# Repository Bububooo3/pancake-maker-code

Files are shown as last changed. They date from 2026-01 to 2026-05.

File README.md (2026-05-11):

# AUTOMATIC PANCAKE MAKER

## JACKSON LOSSIUS, RICHARD SCOTT

---

final product

---

<details>
  <summary>See Video Demo</summary>
  
  https://github.com/user-attachments/assets/425521ff-0307-458f-a22e-615c610f6d97
  
  </details>

<br>

[See electrical diagram](https://github.com/Bububooo3/Automatic-Pancake-Maker/blob/main/Diagrams/Pancake%20Maker%20Wiring%20Diagram.pdf)

---

> [!NOTE]
> For this project, we designed and constructed a machine that takes in batter and produces pancakes. The machine dispenses batter onto a heated conveyor belt, which moves the batter towards the exit slot based on a timer. A heated top conveyor belt above the pancake works with the heated conveyor on the bottom to squeeze the pancake and dispense it through this slot. The machine is well-insulated, and Arduino-driven electrical work can be concentrated below or next to the product. A user-interface on the machine lets users know what is happening and what they need to do using an LED strip and a LCD display.

---

# PROJECT OVERVIEW

> [!IMPORTANT]
> We’re providing a solution for hungry, busy engineering students and teachers who lack time to make food. Students can come early, stay late, and stay on task without leaving the lab for food breaks. Being able to make pancakes efficiently with a machine will help the Engineering Lab and Robotics team raise money through sales.

## Design Goals

- 1 pancake every 60 seconds  
- 20 minutes continuous functionality minimum  
- Insulation  
- Electronics must be sealed  
- Consistent size  
- Effective user interface  
- Fully cooked  
- Minimize burnt pancakes and debris  

## Constraints

- Time: must be completed by April 26th  
- Budget: must be inside a $800.00 budget  
- Space: must fit in the lab  
- Safety: must be properly contained, so it will not be a fire or electrical hazard  
- Must weigh less than 25 kg  

---

# RESOURCES

## POPCAKE

> We referenced the site and manual for the Popcake machine, which is a commercial pancake-maker sold mainly to hotels for $3000/unit.

## YOUTUBE

> We referenced YouTube videos to learn about electrical components, mechanical concepts, and using Arduino boards.

## AI

> We referenced AI (Anthropic’s Claude and Microsoft’s Copilot) to locate logic errors during the tedious and vital debugging process. While planning wiring, we used AI to help ensure safe design and make up for unfamiliarity with electrical engineering.

## ARTICLES & FORUMS

> We referenced online articles and forums regularly to sort out wiring issues, learn overall best practices, and develop design concepts.

## PROFESSIONALS

> We consulted our teacher, Mr. Fennesy, for guidance in all stages of the production process: researching, designing, building, and testing/iterating. Meeting with an engineer from Popcake helped us understand their machine and design an effective one ourselves. Our project mentor Mr. Wingfield helped us ensure our electrical work is safe and functional.

---

# LEARNED SKILLS

## JACKSON

- Researching and designing products  
- Technical drawings  
- Iterative design  
- Mechanical assembly  
- Operating belt sander, drill press, band saw, and other tools  

## RICHARD

- Embedded systems programming  
- Planning and constructing circuits  
- Identifying electrical components  
- Researching and designing products  
- Electrical safety procedures  

---

# CHALLENGES

- After choosing the project, conducting research was challenging, because there were not many existing automatic pancake makers to reference, and Popcake is very protective of product information.  
- Planning wiring and realizing that plan were both long and challenging iteration processes.  
- Designing the product was a challenging process. To avoid having to spend a large amount of time mastering CAD software, Jackson took advantage of his artistic skills to create technical drawings.  
- Ensuring user safety and maximizing cost efficiency were both challenging goals to achieve.  

---

# EVALUATION & ANALYSIS

## REFLECTION

> Like many of the projects, this automatic pancake-maker was a struggle to make from start to finish. Neither of us could’ve done it alone. Because of this struggle, every accomplished task felt like it was worth celebrating, and enduring and adapting to the process head-on meant getting to learn everything the project required of us by ourselves. Above all, it was an amazing learning experience and successful collaboration.

## MISTAKES

- Taking our time at the start  
- Going long periods doing respective tasks without communicating progress to each other  
- Waiting until the last week to build and test the final product  
- Procrastinating on tasks that seemed too difficult to accomplish  
- Forgetting to set the potentiometer on electrical components, resulting in smoke, melting, and explosions on multiple occasions.  
- Underestimating the project’s difficulty  
- Avoiding using AI to debug until there was little time left to code.  

---

# MECHANICAL BILL OF MATERIALS

- MyLifeUNIT Pancake Batter Dispenser, 40oz  
- Presto 07071 15-inch Electric Tilt-n-fold Griddle, Black  
- Amazon Grocery, Original Pancake and Waffle Mix, 32 oz  
- Betty Crocker Bisquick Shake 'n Pour, Buttermilk Pancake Mix, 5.1 oz  
- Krusteaz Light and Fluffy Buttermilk Complete Pancake Mix, Waffle and Pancake Mix, Just Add Water, 32 oz Box  
- Hungry Jack Complete Extra Light and Fluffy Pancake Mix and Waffle Mix, 32 oz Box  
- Great Value Complete Pancake & Waffle Mix, Extra Fluffy, Original, 32 oz  
- 24t x 15mm Wide Aluminum Pulley (HTD 5mm, 8mm1/2" hex Bore) (WCP-1803)  
- belts  
- bearings  
- Bearing plates  
- ceramic fireproof insulation  
- (Economy Geared Stepper Motor) Alloy Steel Mounting Bracket ST-M1  
- Mrs. Butterworth's Complete Buttermilk Pancake Mix, 32 oz  
- 3 Pack PTFE Teflon Sheet 16"x20"  
- Mrs. Butterworth's Complete Buttermilk Pancake Mix, 32 oz  
- Betty Crocker bisquick pancake mix  
- Mainstays 4 Cup PP Plastic Measuring Cup, 32 oz, Clear  
- Great Value Complete Pancake & Waffle Mix, Buttermilk, 32 oz  
- Mainstays Solid Kitchen Turner, Nylon, Black, Diamond Pattern Handle  
- GoodCook 4 Quart Stainless Steel Mixing Bowl  
- GoodCook Pro Measuring Cups And Spoons, Set Of 8 Nesting With Storage Ring  
- motor shaft adaptor to hex (shaft coupler)  
- 0.5 in. 7075 Aluminum Hex Shaft Stock. 3' x2  
- compliance wheels for conveyor belt  
- Steel supports  
- food grade high temp silicone  
- 10 pack ptfe sheets 12"x16"  
- high temp epoxy  
- Bonded #92 TeflonThread - UV Resistant and Heavy Duty Heat-Low Temperature Resistant Thread Sewing - Extra Strong Outdoor Thread - Can Be Used On Home Sewing Machine 600yds (White)

---

# ELECTRICAL BILL OF MATERIALS

- Heat Paste  
- Extension Cord  
- 220 Ω Resistor (In kit)  
- 470 Ω Resistor (In kit)  
- 1000 μF Capacitors (Capacitor Kit)  
- 100 μF Capacitors (In kit)  
- 12V DC Power Supply  
- Buck Converter (LM2596)  
- Solid State Relay  
- Dial Potentiometer Kit  
- Wago Connector Kit  
- Barrel Screw Adapter  
- In-line Fuse Holder  
- Nuts  
- Jumper Wires  
- Diodes  
- LCD 1602 (Standard Config)  
- MyLifeUNIT Pancake Batter Dispenser, 40oz  
- STEPPERONLINE NEMA 17 Stepper Motor (Economy Geared Stepper Motor) Alloy Steel Mounting Bracket ST-M1  
- Arduino Microcontroller  
- STEPPERONLINE NEMA 17 Stepper Motor (Economy Geared Stepper Motor) Alloy Steel Mounting Bracket ST-M1  
- 1 kΩ Resistor (Resistor Kit)  
- NeoPixel 8 LED Strip (WS2812B)  
- Arduino Mega 2560 (x2)  
- A4988 Stepper Motor Driver (w/ Heat Sinks)  
- Push Button Kit  
- LCD 1602 (Standard Config)  
- Star Washers  
- Ring Terminals  
- Flat Washers  
- Breadboards  

---

# MATH & PHYSICS INVOLVED

- Rotational Kinematics  
- Geometry  
- Arithmetic

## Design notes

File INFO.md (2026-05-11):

<h2>Automatic Pancake Maker</h2>

My first Arduino/electrical project! 

> Simulator diagrams don't match real thing, bc sims don't have necessary components or capabilities

View up-to-date hand-drawn diagram [here](https://github.com/Bububooo3/Automatic-Pancake-Maker/blob/main/Diagrams/Pancake%20Maker%20Wiring%20Diagram.pdf)

<hr>
  I did mostly electrical and software stuff and my partner Jackson does mostly mechanical and product design stuff. We worked together on a lot of stuff, too.
<hr>
<h3>Power Diagram</h3>

https://github.com/Bububooo3/pancake-maker-code/blob/main/Pancake%20Maker%20Electronic%20Diagram.pdf

<hr>
<h3>Wokwi ("Current" system)</h3>

https://wokwi.com/projects/449513725919513601

> Prototype: https://wokwi.com/projects/454495520037891073
>
> TinkerCAD: [(Outdated)](https://www.tinkercad.com/things/4bpHhnqHLCV-subsystem-wiring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)

<hr>

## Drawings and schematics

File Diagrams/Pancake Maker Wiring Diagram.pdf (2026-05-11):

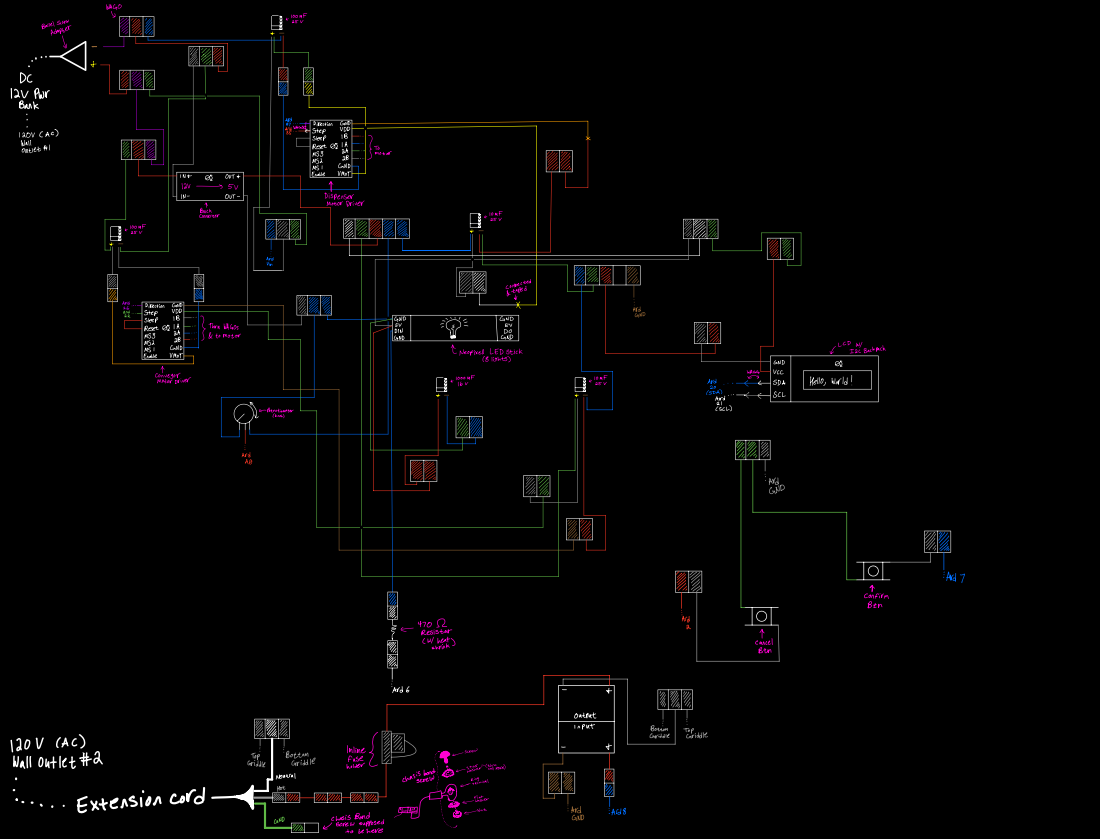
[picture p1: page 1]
Adapter; cPwr; askand; ND viaIB1Aat; unotDirection; step sleep reset mss mss enane us; I orIac; HetI; motor to; connerDriverBuck; one; suroom; Ara andand ND viaIB1Aat; GND; step sleep reset mss mss; enanex; and; inandANDso GND.turn; Do WAGos; Law LEDstick; Barrackneopixes; Iac islists andwaao.weconveyor notondriverroom; one suand; mar 2 And ascusHello a; world SDAcc; I sa potentiometer; can; Arato; Ard GND; Ard; confirm Ben; right left 1; vdots; nor; Adr; resistor; cutneat; shrinkcancel; Btn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

wagoroom suBarrel screw

inr V21in.outsoout.Dispenser motor
atomotor

vi.connected taped

output
Bottom Griddleinput Gridaetop

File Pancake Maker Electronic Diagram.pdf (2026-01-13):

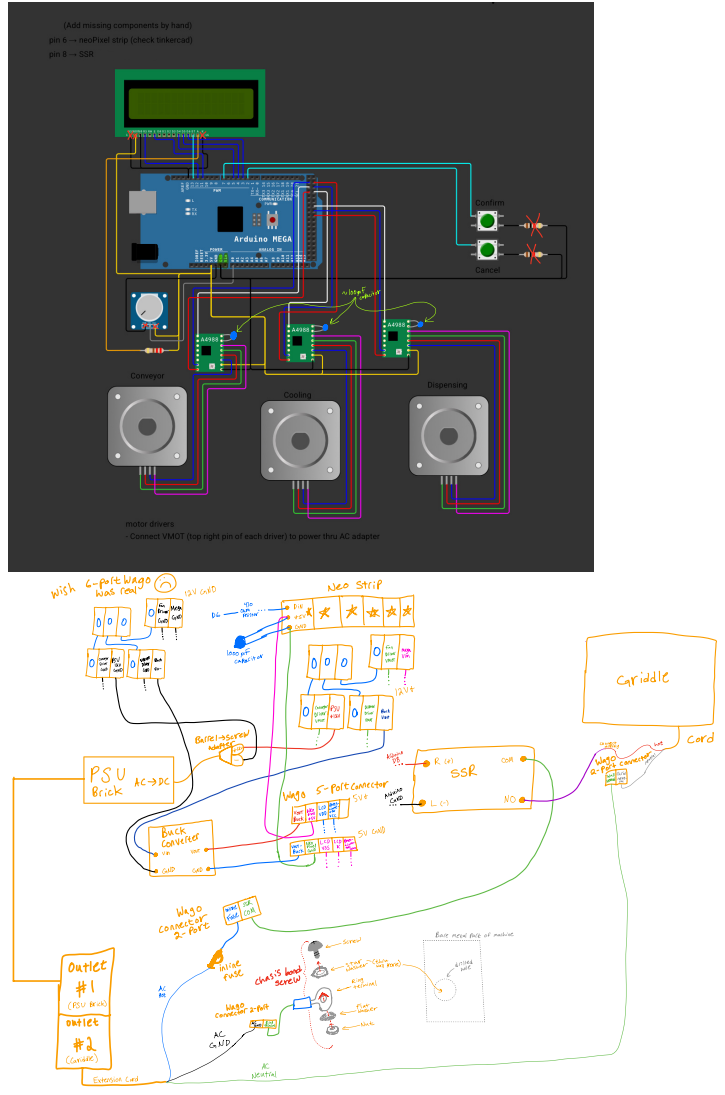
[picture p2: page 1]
lowdose; Paridae; III; neutral

wish68 ¹⁹,90
IBi.li iiIo.F iiiIii
Iii tiIiii
iiiiiiiii'itife.ae
isiii iiii
iIii
IEi

IiiiiiIiiii ii.it
iiiiiii ii

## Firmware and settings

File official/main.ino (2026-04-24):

#include <Adafruit_NeoPixel.h>
#include <LiquidCrystal_I2C.h>
#include <AccelStepper.h>
#include <Wire.h>

#include "Animations.h"
#include "Pins.h"
#include "Motors.h"
#include "Times.h"
#include "States.h"



/////////////////
/// VARIABLES ///
/////////////////
///////////////////////////////////////////////////////////////////////////////////////////
// Booleans //
bool confirmPressedPrev = LOW, cancelPressedPrev = LOW;  // Init button states
bool dispensingActive = false;                           // Init dispenser states
bool serviceMsg = false;                                 // Init service message state
bool griddleEnabled = false;                             // Init griddle state
bool griddleReady = true;                                // Init griddle state
bool griddleReadyPrev = true;                            // exactly what it sounds like
bool confirmStable = LOW;                                // more reliable input
bool cancelStable = LOW;                                 // more reliable input
bool tkA = false;                                        // is kill mode active
bool dispenserHoming = false;                            // is dispenser homing
bool heatOnBoot = true;                                  // Config
bool firstCake = false;
bool lastCake = false;

// Strings //
String lastPrintLCD1 = "";
String lastPrintLCD2 = "";
String placeholder = "                ";

// State Machine //
Status status = STATUS_REQUEST;

// Numbers //
int mlevel = 8;     // Maximum # pancakes we're able to make
int level = 1;      // Init # pancakes to make
int plevel = 0;     // Init previous # pancakes to make
int dispensed = 0;  // Init # pancakes dispensed

unsigned long t_bake, t_kill, t_griddle, t_dispense, t_confirmDebounce, t_cancelDebounce, t_lastCake;  // Init timers


//////////////////
/// COMPONENTS ///
//////////////////
///////////////////////////////////////////////////////////////////////////////////////////
// Initialize LCD: (Address, Column, Rows)
LiquidCrystal_I2C lcd(0x27, 16, 2);

// Initialize LED Strip: (#LEDs, Pin, Color Mode + Signal)
Adafruit_NeoPixel led(8, LEDPIN, NEO_GRB + NEO_KHZ800);

// Initialize stepper motors: (driver, STEP, DIR)
AccelStepper conveyor(AccelStepper::DRIVER, CONVEYORPIN_STEP, CONVEYORPIN_DIR);
AccelStepper dispenser(AccelStepper::DRIVER, DISPENSERPIN_STEP, DISPENSERPIN_DIR);
/* AccelStepper fan(AccelStepper::DRIVER, 25, 23); */

///////////////////////////////////////////////////////////////////////////////////////////



////////////////////////////////////
/// LIBRARY-DEPENDENT CONSTANTS ////
////////////////////////////////////
///////////////////////////////////////////////////////////////////////////////////////////
// Colors
#define WHITE led.Color(255, 255, 255)
#define RED led.Color(255, 0, 0)
#define GREEN led.Color(0, 255, 0)
#define BLUE led.Color(0, 0, 255)
#define YELLOW led.Color(255, 255, 0)
#define CYAN led.Color(0, 255, 255)
#define MAGENTA led.Color(255, 0, 255)
#define ORANGE led.Color(255, 165, 0)
#define PURPLE led.Color(128, 0, 128)
#define OFF 0

// Presets
const uint32_t warning[8] = { YELLOW, ORANGE, YELLOW, ORANGE, YELLOW, ORANGE, YELLOW, ORANGE };
const uint32_t danger[8] = { RED, RED, RED, RED, RED, RED, RED, RED };
const uint32_t rqst[8] = { PURPLE, MAGENTA, PURPLE, MAGENTA, PURPLE, MAGENTA, PURPLE, MAGENTA };
const uint32_t dormant[8] = { BLUE, WHITE, BLUE, WHITE, BLUE, WHITE, BLUE, WHITE };
const uint32_t off[8] = { OFF, OFF, OFF, OFF, OFF, OFF, OFF, OFF };
const uint32_t valid[8] = { GREEN, GREEN, GREEN, GREEN, GREEN, GREEN, GREEN, GREEN };
uint32_t prevLED[8] = { OFF, OFF, OFF, OFF, OFF, OFF, OFF, OFF };

////////////////////////////////////////////////////////////////////////////////////////



/////////////////
/// FUNCTIONS ///
/////////////////
////////////////////////////////////////////////////////////////////////////////////////////
// Macros
#define getArraySize(a) (sizeof(a) / sizeof((a)[0]))

// Center/truncate string (16 characters)
String center(String msg) {
  return (msg.length() <= 16) ? placeholder.substring(0, (16 - msg.length()) / 2) + msg : msg.substring(0, 16);
}


// Display string on LCD
bool printMessage(String msg, int line = 0) {
  if (line) {
    if (lastPrintLCD2 == msg) {
      return false;
    }
  } else {
    if (lastPrintLCD1 == msg) {
      return false;
    }
  }

  line = constrain(line, 0, 1);
  lcd.setCursor(0, line);
  lcd.print(placeholder);
  lcd.setCursor(0, line);
  lcd.print(msg);

  if (line) {
    lastPrintLCD2 = msg;
  } else {
    lastPrintLCD1 = msg;
  }

  return true;
}


// Clear LCD line or entire screen if no params
bool clearLine(int lvl = -1) {
  if (lvl < 0) {
    lcd.clear();
    lastPrintLCD1 = "";
    lastPrintLCD2 = "";
    return true;
  }

  lvl = constrain(lvl, 0, 1);
  printMessage(placeholder, lvl);
  return true;
}


// Return whether the previous LED is the same as the current one
bool getLEDUnchanged(const uint32_t a[]) {
  return (
    prevLED[0] == a[0] && prevLED[1] == a[1] && prevLED[2] == a[2] && prevLED[3] == a[3] && prevLED[4] == a[4] && prevLED[5] == a[5] && prevLED[6] == a[6] && prevLED[7] == a[7]);
}

void setLEDChanged(const uint32_t a[]) {
  prevLED[0] = a[0];
  prevLED[1] = a[1];
  prevLED[2] = a[2];
  prevLED[3] = a[3];
  prevLED[4] = a[4];
  prevLED[5] = a[5];
  prevLED[6] = a[6];
  prevLED[7] = a[7];
}


// Set LED strip colors manually
bool setColors(int a = OFF, int b = OFF, int c = OFF, int d = OFF, int e = OFF, int f = OFF, int g = OFF, int h = OFF) {
  led.setPixelColor(0, a);
  led.setPixelColor(1, b);
  led.setPixelColor(2, c);
  led.setPixelColor(3, d);
  led.setPixelColor(4, e);
  led.setPixelColor(5, f);
  led.setPixelColor(6, g);
  led.setPixelColor(7, h);

  uint32_t temp[8] = { a, b, c, d, e, f, g, h };
  setLEDChanged(temp);

  led.show();
  return true;
}


// Set LED strip colors using a preset
bool floodColors(const uint32_t z[8]) {
  setColors(z[0], z[1], z[2], z[3], z[4], z[5], z[6], z[7]);
  return true;
}


// Disable LED strip lights efficiently
bool disableLED() {
  led.setPixelColor(0, OFF);
  led.setPixelColor(1, OFF);
  led.setPixelColor(2, OFF);
  led.setPixelColor(3, OFF);
  led.setPixelColor(4, OFF);
  led.setPixelColor(5, OFF);
  led.setPixelColor(6, OFF);
  led.setPixelColor(7, OFF);
  led.show();
  return true;
}


// Set fan motor pulse rate
void setFanPower(float i) {
  // <disabled> fan.setSpeed(MAXSTEP * constrain(i, 0, 1));
}


// Get the net difference between these two times in milliseconds
unsigned long difftime(unsigned long t1, unsigned long t2) {
  return (t2 >= t1) ? (t2 - t1) : (0xFFFFFFFFUL - t1 + t2 + 1);  // ~49-day lifetime of accuracy
}

////////////////////////////////////////////////////////////////////////////////////////



/////////////////
// ABSTRACTION //
/////////////////
////////////////////////////////////////////////////////////////////////////////////////////
// EXTRA INTERFACE CONSTANTS (for optimization, convenience & such)
const String spsMsg = "Pancakes";  // Word to show for >1 pancakes
const String amt = "Auto-Mode";    // Word to show for auto mode

const String bMsg = center("Baking");

const String eMsg1 = center("Action");      // Cancel display line 1
const String eMsg2 = center("Terminated");  // Cancel display line 2

const String rMsg1 = center("Pancakes");
const String rMsg2 = center("Ready");

void bakeComplete();  // Just in case

// QoL method
bool isActive(Status check) {
  return (status == check);
}

void setActive(Status check) {
  status = check;
}

// Display a message on LCD asking for # pancakes (and set requesting to true simultaneously)
void requestNumPancakes() {
  setActive(STATUS_REQUEST);
  printMessage(center("Bake how many?"));
  clearLine(1);
}


// Set whether the griddle should be heating up or cooling down or neither
void setGriddleEnabled(bool enabled) {
  if (griddleEnabled == enabled) {
    return;
  }

  digitalWrite(GRIDPIN, enabled);
  griddleEnabled = enabled;
  griddleReady = false;
  t_griddle = millis();
}


// Update griddle per heartbeat w/o yielding program
// Returns true if griddle is fully cooled or heated
bool updateGriddle() {
  unsigned long elapsed = difftime(t_griddle, millis());
  bool canWriteLCD = !isActive(STATUS_READY) && !isActive(STATUS_CANCEL);

  if (griddleEnabled) {
    if (canWriteLCD) {
      int frame = static_cast<int>(elapsed / ANIMINC) % getArraySize(heatingAnim);
      printMessage(center(heatingAnim[frame]), 1);
    }
    if (!griddleReady && elapsed >= HEATUP) {
      griddleReady = true;
      if (isActive(STATUS_BAKE)) t_dispense = millis();
      return true;
    }
  } else {
    if (canWriteLCD) {
      int frame = static_cast<int>(elapsed / ANIMINC) % getArraySize(coolingAnim);
      printMessage(center(coolingAnim[frame]), 1);
    }
    if (!griddleReady && elapsed >= COOLDOWN) {
      griddleReady = true;
      return true;
    }
  }
  return false;
}

// The entire warm-up process for the machine w/ animations
void introductionProtocol() {
  for (int i = 0; (i < getArraySize(intro)); i++) {
    printMessage(center(intro[i]));
    delay(ANIMINC);
  }

  printMessage(center("By Jesuit HS"), 1);
  delay(MSGWAIT);
  clearLine();

  setFanPower(1.0f);

  if (heatOnBoot) {
    setGriddleEnabled(true);
  }

  printMessage(center("[Complete]"), 1);
  delay(MSGWAIT);
  clearLine();
}


// For handling during cancel state or errors
void homeDispenser() {
  dispensingActive = false;
  dispenserHoming = true;
  dispenser.moveTo(DISPENSERCLOSE);
}

// Dispense pancakes fxn
bool dispense() {
  if (dispenserHoming) {
    if (dispenser.distanceToGo() == 0 && dispenser.currentPosition() == DISPENSERCLOSE) {
      dispenserHoming = false;
    }
    return false;
  }

  if (!dispensingActive) return false;

  if (dispensed >= level) return false;

  if (dispenser.distanceToGo() == 0) {
    if (dispenser.currentPosition() == DISPENSEROPEN) {
      dispenser.moveTo(DISPENSERCLOSE);
    } else if (dispenser.currentPosition() == DISPENSERCLOSE) {
      dispensingActive = false;
      dispenser.setCurrentPosition(dispenser.currentPosition());
      return true;
    }
  }
  return false;
}


// Handle the confirm/cancel button logic
void handleButtons() {
  bool rawConfirm = (digitalRead(CONFIRMPIN) == LOW);
  bool rawCancel = (digitalRead(CANCELPIN) == LOW);

  unsigned long now = millis();

  // CONFIRM DEBOUNCE
  if (rawConfirm != confirmStable) {
    if (now - t_confirmDebounce >= DEBOUNCE) {
      confirmStable = rawConfirm;
      t_confirmDebounce = now;  // Reset only after committing
    }
  }

  // CANCEL DEBOUNCE
  if (rawCancel != cancelStable) {
    if (now - t_cancelDebounce >= DEBOUNCE) {
      cancelStable = rawCancel;
      t_cancelDebounce = now;  // Reset only after committing
    }
  }

  bool confirmPressed = confirmStable;
  bool cancelPressed = cancelStable;

  // Confirm button pressed
  if (!confirmPressedPrev && confirmPressed) {
    switch (status) {
      case STATUS_CANCEL:
        setActive(STATUS_REQUEST);
        t_kill = 0;
        tkA = false;
        lastCake = false;
        clearLine();
        printMessage(center("[please wait]"));
        plevel = -1;
        break;

      case STATUS_REQUEST:
        level = map(analogRead(A0), 0, 1023, 1, mlevel);
        if (!heatOnBoot) setGriddleEnabled(true);

        t_bake = now;
        t_dispense = now;
        griddleReadyPrev = false;
        dispensingActive = false;
        dispenserHoming = false;
        lastCake = false;
        dispensed = 0;

        clearLine();
        firstCake = true;
        setActive(STATUS_BAKE);
        break;

      case STATUS_READY:
        setActive(STATUS_REQUEST);
        break;
    }
  }

  // Cancel button pressed
  if (cancelPressed && !cancelPressedPrev) {
    setActive(STATUS_CANCEL);

    if (!heatOnBoot) {
      setGriddleEnabled(false);
    }

    homeDispenser();
    clearLine();
    t_kill = millis();
    tkA = true;
    lastCake = false;
    t_confirmDebounce = millis();
  }

  // Baking System
  conveyor.setSpeed(isActive(STATUS_BAKE) ? CONVEYORSTEP : 0);
  // <disabled> fan.setSpeed(isActive(STATUS_BAKE) ? MAXSTEP : 0);

  // Store state
  confirmPressedPrev = confirmPressed;
  cancelPressedPrev = cancelPressed;
}


void updateMotors() {
  conveyor.runSpeed();
  bool cycleComplete = dispense();
  dispenser.run();

  if (!griddleReady) {
    updateGriddle();
    griddleReadyPrev = false;
  } else {
    griddleReadyPrev = true;
  }

  serviceMsg = !griddleReady;

  if (!isActive(STATUS_BAKE)) return;

  if (cycleComplete) {
    dispensed++;
    t_dispense = millis();

    if (level < mlevel && dispensed >= level) {
      lastCake = true;
      t_lastCake = millis();
      return;
    }
  }

  if (lastCake && difftime(t_lastCake, millis()) >= COOKTIME) {
    lastCake = false;
    bakeComplete();
    return;
  }

  if (level == mlevel && difftime(t_bake, millis()) >= AUTOTIMEOUT) bakeComplete();
}

// Update per heartbeat fxn
void heartbeat() {
  t_bake = isActive(STATUS_BAKE) ? t_bake : 0UL;
  t_dispense = isActive(STATUS_BAKE) ? t_dispense : 0UL;
  t_kill = (isActive(STATUS_CANCEL) && tkA) ? t_kill : 0UL;

  handleButtons();
  updateMotors();
}


// The screen for asking for pancakes
void requestScreen() {
  // Map 0-1023 :: 1–mlevel
  level = map(analogRead(A0), 0, 1023, 1, mlevel);

  printMessage(center("Bake how many?"));

  // Choose # Pancakes Screen
  if ((abs(level - plevel) >= 1) && isActive(STATUS_REQUEST)) {
    if (level < mlevel) {
      printMessage(center(String(level * 2) + " " + spsMsg), 1);
    } else {
      printMessage(center(amt), 1);
    }

    plevel = level;
  }
}


// Runs when baking is finished
void bakeComplete() {
  setActive(STATUS_READY);
  if (!heatOnBoot) {
    setGriddleEnabled(false);
  }
}

// Display while baking
void bakeScreen() {
  if (!griddleReadyPrev) {
    printMessage(center("Heating..."));
    return;
  }

  printMessage(bMsg);
  printMessage((level < mlevel) ? center(String(level * 2) + " " + spsMsg) : center(amt), 1);

  if (!lastCake && ((firstCake) || (!dispensingActive && !dispenserHoming && (difftime(t_dispense, millis()) >= COOKTIME)))) {
    firstCake = false;
    dispensingActive = true;
    dispenser.moveTo(DISPENSEROPEN);
  }
}

// Display for when the pancakes are ready
void readyScreen() {
  printMessage(rMsg1);
  printMessage(rMsg2, 1);
}

////////////////////////////////////////////////////////////////////////////////////////



/////////////
// RUNTIME //
/////////////
////////////////////////////////////////////////////////////////////////////////////////
// Run once on boot
void setup() {
  // Pin Initialization
  pinMode(CONFIRMPIN, INPUT_PULLUP);
  pinMode(CANCELPIN, INPUT_PULLUP);
  pinMode(LEDPIN, OUTPUT);
  pinMode(GRIDPIN, OUTPUT);

  // LCD
  lcd.init();
  lcd.backlight();

  // LED
  led.begin();
  led.show();
  introductionProtocol();

  // Serial.begin(9600);

  // Stepper Motors
  conveyor.setMaxSpeed(CONVEYORSTEP);
  conveyor.setAcceleration(400);
  digitalWrite(CONVEYORPIN_DIR, ((CONVEYOR_INVERT) ? HIGH : LOW));
  digitalWrite(DISPENSERPIN_DIR, ((DISPENSER_INVERT) ? HIGH : LOW));
  // <disabled> fan.setMaxSpeed(MAXSTEP);
  dispenser.setMaxSpeed(DISPENSERSPEED);
  dispenser.setAcceleration(DISPENSERACCEL);

  dispenserHoming = true;
  dispenser.setCurrentPosition(dispenser.currentPosition());
  // while (dispenser.distanceToGo() != 0) dispenser.run();
  dispenserHoming = false;

  // Initialize griddle bc of heatOnBoot
  griddleReadyPrev = griddleReady;
}


// Run repeatedly
void loop() {
  heartbeat();

  // Light handling
  switch (status) {
    case STATUS_READY:
      // if (getLEDUnchanged(valid)) break;
      floodColors(valid);
      break;

    case STATUS_REQUEST:
      // if (getLEDUnchanged(rqst)) break;
      floodColors(rqst);
      break;

    case STATUS_BAKE:
      // if (getLEDUnchanged(warning)) break;
      floodColors(warning);
      break;

    case STATUS_CANCEL:
      // if (getLEDUnchanged(danger)) break;
      floodColors(danger);
      break;

    case STATUS_EMPTY:
      // if (getLEDUnchanged(dormant)) break;
      floodColors(dormant);
      break;
  }

  // Main logic handling
  if (serviceMsg && !isActive(STATUS_CANCEL) && !isActive(STATUS_BAKE) && !isActive(STATUS_READY)) return;

  switch (status) {
    case STATUS_CANCEL:
      printMessage(eMsg1);
      printMessage(eMsg2, 1);

      if (tkA && difftime(t_kill, millis()) >= KILLTIMEOUT) {
        tkA = false;
        clearLine();
        requestNumPancakes();
      }
      break;

    case STATUS_REQUEST:
      requestScreen();
      break;

    case STATUS_BAKE:
      bakeScreen();
      break;

    case STATUS_READY:
      readyScreen();
      break;

    case STATUS_EMPTY:
      requestNumPancakes();
      break;

    default:
      setActive(STATUS_EMPTY);
      break;
  }
}

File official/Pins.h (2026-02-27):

#ifndef PINS_H
#define PINS_H

// Button pins
const int CONFIRMPIN = 7;  // Confirm
const int CANCELPIN = 2;   // Cancel


// Appliance pins
const int LEDPIN = 6;   // For the NeoPixel strip
const int GRIDPIN = 8;  // For the SSR controlling the griddle


// Conveyor pins
const int CONVEYORPIN_STEP = 22;  // Step
const int CONVEYORPIN_DIR = 26;   // Direction


// Dispenser pins
const int DISPENSERPIN_STEP = 35;  // Step
const int DISPENSERPIN_DIR = 37;   // Direction

#endif

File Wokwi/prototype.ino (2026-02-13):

#include <Adafruit_NeoPixel.h>
#include <LiquidCrystal_I2C.h>
#include <AccelStepper.h>
#include <Wire.h>

/*
  PINS

  LCD w/ I2C Backpack:
	VCC 	→ 	5V
  GND 	→ 	GND
  SDA 	→ 	20
  SCL 	→ 	21


  Knob Potentiometer:
	GND		→		GND
	SIG		→		A0
	VCC		→		5V


  Conveyor Driver <Conveyor Stepper Motor Pin>:
	EN		→		24
	STEP	→		22
	DIR		→		26

	GND.2	→		GND

	2B		→		<B->
	2A		→		<A->
	1A		→		<A+>
	1B		→		<B+>

	VDD		→		5V
	GND.1	→		GND]


  Confirm Push Button:
	1:1 L	→		7
	1:2 R	→		GND


  Cancel Push Button:
	1:1 L	→		2
	1:2 R	→		GND
*/

/*
 	  ////////////////////////////////
	 // CONCERNING HEATING ELEMENT //
	////////////////////////////////
  ///////////////////////////////////////////////////////////////////////////////////////////
  > TinkerCAD sim doesn't support AC in the way needed for the griddle
  > For the real product, replace MOSFET w/ a solid-state relay (SSR)
  > The DC power supply represents the AC mains
  > Use SSR rated >=15A @ 120V AC
  > Ask mentor/electrician if unsure

  /////////////////////////////////////////////////////
  Reference Link
  > https://shorturl.fm/pwcKO

  /////////////////////////////////////////////////////
  Step-by-step Replacement Process:
  12V DC Power Suppy || 120V AC Outlet
  MOSFET			   ||  Solid-state relay
  - Cut only hot wire of extension cord
  - On the SSR, connect one end to COM & other to NO
  - Griddle turns on when relay is on & off when relay is off
  - DO NOT CUT NEUTRAL WIRE
  - We can control T using PID , maybe if we have time
  	^ (Not a necessity)
    ^ (Using rate of change, current T, target T, & time passed)

  /////////////////////////////////////////////////////
  Griddle Details (1200 Watt)
  > 2 prongs/wires (non-grounded)
  - Narrow blade: Hot(live) --> often black
  - Wide blade: Neutral --> often white
  > Hot wire carries 120V AC
  - Use an extension cord. Don't cut griddle cord directly.
  - Cut cord jacket carefully & strip hot wire after cutting it.

*/



/////////////
// GLOBALS //
/////////////
///////////////////////////////////////////////////////////////////////////////////////////
// bool baking = false, requesting = false, cancelMode = false, ready = false;
bool confirmPressedPrev = LOW, cancelPressedPrev = LOW;
bool griddleEnabled = false, griddleReady = true, heatOnBoot = false, serviceMsg = false;
String lastPrintLCD1 = "";
String lastPrintLCD2 = "";
String placeholder = "                ";
int level = 1;
int plevel = 0;
int dispensed = 0;
unsigned long t_bake, t_kill, t_griddle, t_dispense;

///////////////////////////////////////////////////////////////////////////////////////////


///////////////
// CONSTANTS //
///////////////
///////////////////////////////////////////////////////////////////////////////////////////
// Counts
// #define LEDCOUNT 8

// Time Lengths (milliseconds)
#define HEATUP 2e3
#define COOLDOWN 2e3
#define KILLTIMEOUT 60e3
#define MSGWAIT 1.5e3
#define ANIMINC 0.25e3
#define COOKTIME 10e3

// Step pulse rate (steps/second)
#define MAXSTEP 800.0
#define CONVEYORSTEP 800.0
// #define DISPENSERSPEED 800.0
// #define DISPENSERACCEL 400.0

// Step positions (Usually 1.8°/step, 200 steps/revolution)	← <Research more based on specific motor>
#define DISPENSEROPEN 0
#define DISPENSERCLOSE 0

// Dispenser states
#define OPENING true
#define CLOSING false

// Buttons
#define CONFIRMPIN 7
#define CANCELPIN 2

// Appliances
// #define LEDPIN 6
// #define GRIDPIN 8
#define CONVEYORPIN_EN 24
// #define COOLINGPIN_EN 27
// #define DISPENSERPIN_EN 33


// State Machine
enum Status {
  STATUS_EMPTY,
  STATUS_REQUEST,
  STATUS_BAKE,
  STATUS_CANCEL,
  STATUS_READY
};

Status status = STATUS_EMPTY;

// Fixed-Size Arrays
const char intro[][16] = {
  "pancake maker",
  "pAncake maker",
  "paNcake maker",
  "panCake maker",
  "pancAke maker",
  "pancaKe maker",
  "pancakE maker",
  "pancake Maker",
  "pancake mAker",
  "pancake maKer",
  "pancake makEr",
  "pancake makeR",
  " ",
};

const char heatingAnim[][16] = {
  "heating",
  "heating.",
  "heating..",
  "heating...",
  "heating",
};

const char coolingAnim[][16] = {
  "cooling",
  "cooling.",
  "cooling..",
  "cooling...",
  "cooling",
};
///////////////////////////////////////////////////////////////////////////////////////////




///////////////////////////
// INITIALIZE COMPONENTS //
///////////////////////////
///////////////////////////////////////////////////////////////////////////////////////////
// Initialize LCD: (RS, E, D4, D5, D6, D7)
// Initialize LED Strip: (#LEDs, Pin, Color Mode + Signal)
// Initialize stepper motors: (driver, STEP, DIR)

LiquidCrystal_I2C lcd(0x27, 16, 2);
// Adafruit_NeoPixel led(LEDCOUNT, LEDPIN, NEO_GRB + NEO_KHZ800);
AccelStepper conveyor(AccelStepper::DRIVER, 22, 26);
// <disabled> AccelStepper fan(AccelStepper::DRIVER, 25, 23);
// AccelStepper dispenser(AccelStepper::DRIVER, 35, 37);

///////////////////////////////////////////////////////////////////////////////////////////



////////////////////////////////
// LIBRARY-SPECIFIC CONSTANTS //
////////////////////////////////
///////////////////////////////////////////////////////////////////////////////////////////
/*
// Colors
#define WHITE led.Color(255, 255, 255)
#define RED led.Color(255, 0, 0)
#define GREEN led.Color(0, 255, 0)
#define BLUE led.Color(0, 0, 255)

#define YELLOW led.Color(255, 255, 0)
#define CYAN led.Color(0, 255, 255)
#define MAGENTA led.Color(255, 0, 255)
#define ORANGE led.Color(255, 165, 0)
#define PURPLE led.Color(128, 0, 128)

#define OFF 0

// Presets
const uint32_t warning[8] = { YELLOW, ORANGE, YELLOW, ORANGE, YELLOW, ORANGE, YELLOW, ORANGE };
const uint32_t danger[8] = { RED, RED, RED, RED, RED, RED, RED, RED };
const uint32_t rqst[8] = { PURPLE, MAGENTA, PURPLE, MAGENTA, PURPLE, MAGENTA, PURPLE, MAGENTA };
const uint32_t dormant[8] = { BLUE, WHITE, BLUE, WHITE, BLUE, WHITE, BLUE, WHITE };
const uint32_t off[8] = { OFF, OFF, OFF, OFF, OFF, OFF, OFF, OFF };
const uint32_t valid[8] = { GREEN, GREEN, GREEN, GREEN, GREEN, GREEN, GREEN, GREEN };
uint32_t prevLED[8] = { OFF, OFF, OFF, OFF, OFF, OFF, OFF, OFF };
*/

// Dispenser
bool dispenseState = OPENING, dispensingActive = false;
long dispenseTarget = DISPENSERCLOSE;

////////////////////////////////////////////////////////////////////////////////////////



/////////////////
/// FUNCTIONS ///
/////////////////
////////////////////////////////////////////////////////////////////////////////////////////
// Macros
#define getArraySize(a) (sizeof(a) / sizeof((a)[0]))

// Center/truncate string (16 characters)
String center(String msg) {
  return (msg.length() <= 16) ? placeholder.substring(0, (16 - msg.length()) / 2) + msg : msg.substring(0, 16);
}
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

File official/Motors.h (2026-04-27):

#ifndef MOTORS_H
#define MOTORS_H

// Step pulse rate (steps/second)
const float MAXSTEP = 800.0;

const float CONVEYORSTEP = 350.0;

const bool CONVEYOR_INVERT = true;

const bool DISPENSER_INVERT = false;

const float DISPENSERSPEED = 25.0;

const float DISPENSERACCEL = 100.0;



// Step position offsets (Usually 1.8°/step, 200 steps/revolution)
const int DISPENSEROPEN = -70 * (5.0/9.0); // degrees * -5/9
const int DISPENSERCLOSE = 0;

#endif

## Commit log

2025-11-03 Update pin configurations and add button handling
    Refactor pinMode calls and add button handling logic.
2025-11-04 Integrate LED strip and refactor button handling
    Refactor subsystem controller to integrate LED strip and update button handling.
2025-11-11 Devised electrical plan for heating element. Conducted research.
2025-11-12 ^intro + ^heating-system-notes
2025-11-20 next step: track time terminated
2025-11-25 Refactor timer handling and add fan control
    Refactor timer variables and update logic for baking and fan control.
2025-12-01 Refactor subsystem_controller.ino for clarity and fixes
    Left off on line 235
    [subsystem_controller.ino]
2025-12-01 Update and rename subsystem_wiring.ino to subsystem_wiring.brd
    [subsystem_wiring.brd]
2025-12-02 Refactor button logic and pin configurations
    Refactor button handling and update pin assignments.
2025-12-03 Fix button press handling and update COOKTIME
    Working on dispensing timing
    [subsystem_controller.ino]
2025-12-04 Maybe switch to Arduino Mega
2025-12-08 Switched to Wowki for Mega to use stepper motors (and more pins)
2025-12-08 Add initial diagram.json for circuit design
2025-12-09 Enhance dispenser logic with serviceMsg variable
    Added serviceMsg variable to track dispenser state and modified related functions for improved logic.
2025-12-09 Enhance dispensing functionality in subsystem_controller
    Added dispensing logic and timer for dispensing pancakes.
2026-01-07 Commented out fan code
    might use different motor like a computer fan instead of a bipolar stepper motor
2026-01-12 WIP
    includes LCD, conveyor, dispenser, & buttons
2026-01-28 Changed to use I2C Backpack for LCD
2026-02-10 Update main controller w/ prototype revisions
2026-04-22 Change motor constants from int to unsigned long
2026-04-24 Refactor motor constants to use const float
2026-05-11 Rename Pancake Maker Wiring Diagram.pdf to Diagrams/Pancake Maker Wiring Diagram.pdf
2026-05-11 Update HEATUP and COOLDOWN times in Times.h
